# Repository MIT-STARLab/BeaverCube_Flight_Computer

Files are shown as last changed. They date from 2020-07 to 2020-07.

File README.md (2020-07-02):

# Note
This board is still under test, we will be updating system operational status as tests are completed.

# BFC
The BeaverCube Flight Computer, or CASTOR Pi Board, is an open-source flight computer for CubeSats. Designed for the MIT BeaverCube CubeSat mission, the board supports an imaging payload with 3 cameras over USB as well as subsystem boards over UART, I2C and SPI buses. 

CASTOR Pi Board: CubeSat Atmospheric and Sea-surface Temperature Optical Observation Raspberry Pi Board

# Known Issues, Testing Progress
The BFC rev 1.0 is currently being tested, with rev 2.0 expected to be manufactured and testing started by the end of August 2020. The power system has been characterized under expected loads and is fully operational with no errors detected. The RPI recovery system (see schematic Sheet 3) that controls which RPI is running and SD card is selected has been fully tested, and no errors detected.

The USB hub is currently under test to verify all ports can communicate with the compute module. Additional tests to be completed by mid-July 2020 include running flight software to verify all onboard devices (RTC, IMUs) function nominally, and interfacing the BFC with devices to test external connections including RS-485, TTL UART, I2C, SPI.

Known errors on rev 1.0 that will be fixed in rev 2.0
- SD card MUXs U4, U11, U13, U14 have incorrect footprints. The compute module cannot access the SD card slots.
- The USB line is routed to the incorrect GPIO pin on the compute module. A temporary fix was made to continue testing.

# project
Eagle CAD Project, Board, Schematic files.

# libraries
Ealgle CAD Library files.

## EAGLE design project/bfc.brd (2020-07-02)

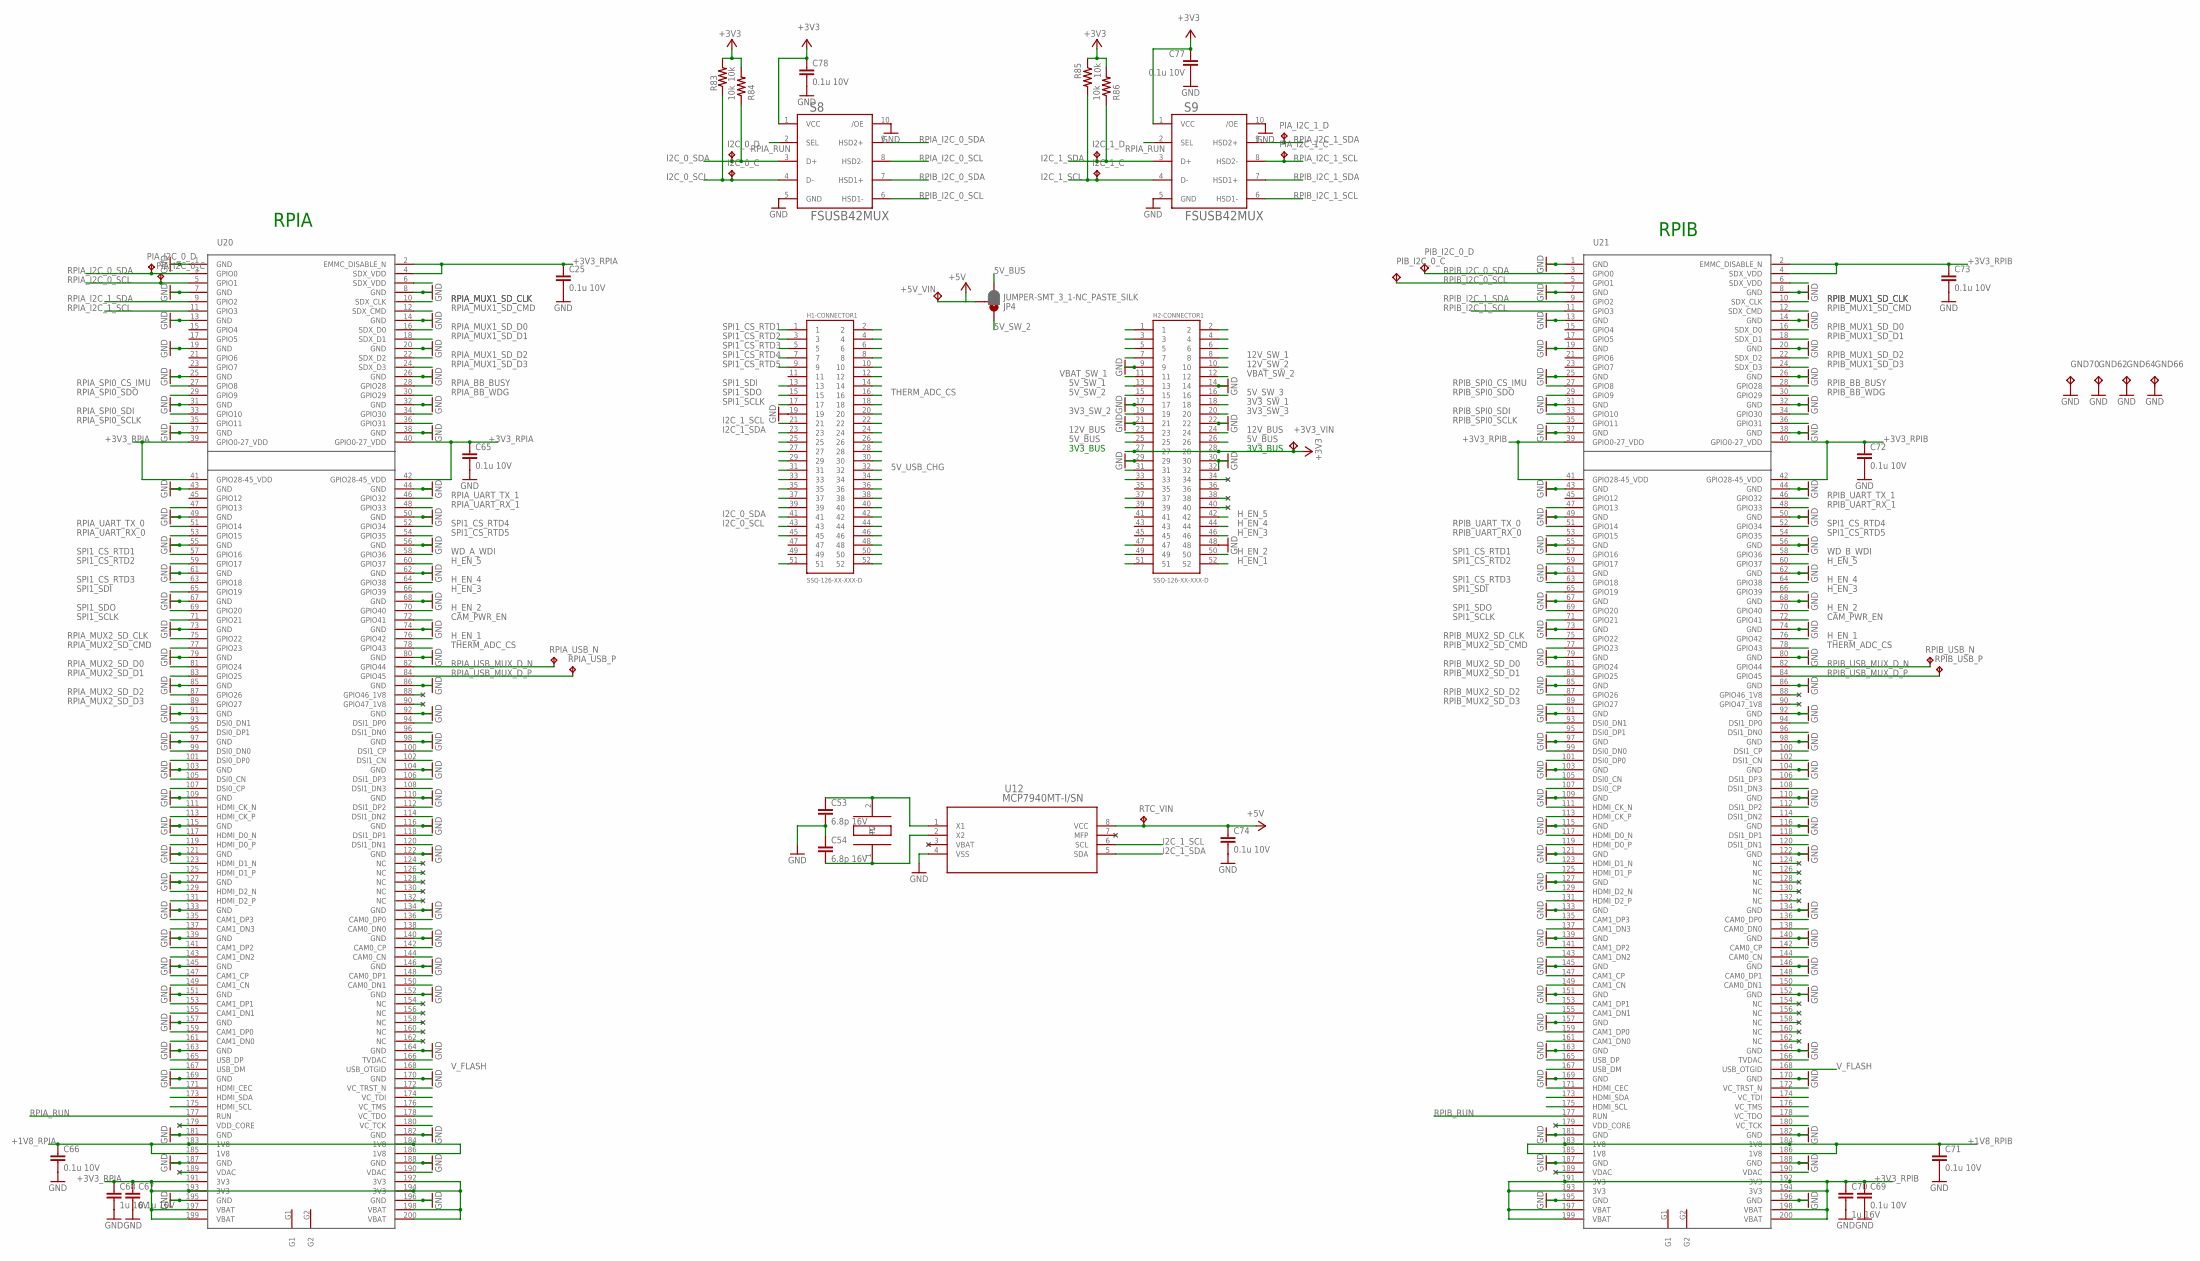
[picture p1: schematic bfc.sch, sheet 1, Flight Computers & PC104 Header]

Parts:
+3V3_VIN, +5V_VIN: TP_HRWN; MPN S2751-46R
C25, C65, C66, C67, C69, C71, C72, C73, C74, C77, C78: 0.1u 10V; C0603
C53, C54: 6.8p 16V; C0603
C68, C70: 1u 16V; C0603
GND62, GND64, GND66, GND70: TP_HRWN; MPN S2751-46R
H1-CONNECTOR1, H2-CONNECTOR1: SSQ-126-XX-XXX-D; MPN SSQ-126-23-G-D
I2C_0_C, I2C_0_D, I2C_1_C, I2C_1_D: TPB1,27; B1,27
JP4: JUMPER-SMT_3_1-NC_PASTE_SILK; SMT-JUMPER_3_1-NC_PASTE_SILK
PIA_I2C_0_C, PIA_I2C_0_D, PIA_I2C_1_C, PIA_I2C_1_D: TPB1,27; B1,27
PIB_I2C_0_C, PIB_I2C_0_D: TP_HRWN; MPN S2751-46R
R83, R84, R85, R86: 10k; R0603
RPIA_USB_N: TPB1,27; B1,27
RPIA_USB_P: TPB1,27; B1,27
RPIB_USB_N: TPB1,27; B1,27
RPIB_USB_P: TPB1,27; B1,27
RTC_VIN: TPB1,27; B1,27
S8, S9: FSUSB42MUX; MPN FSUSB42MUX
U12: MCP7940MT-I/SN; SOIC8-N_MC; MPN MCP7940MT-I/SN
U20, U21: COMPUTE_MODULE; SO-DIMM; MPN 1473005-4
X4: TC-135; MPN FC-135 32.768KA-AG0

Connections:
3V3_SW_1: H2-CONNECTOR1.18
3V3_SW_2: H2-CONNECTOR1.19; also elsewhere on the board
3V3_SW_3: H2-CONNECTOR1.20; also elsewhere on the board
5V_BUS: H2-CONNECTOR1.25, H2-CONNECTOR1.26, JP4.3; also elsewhere on the board
5V_SW_1: H2-CONNECTOR1.13
5V_SW_2: H2-CONNECTOR1.15, JP4.1
5V_SW_3: H2-CONNECTOR1.16
5V_USB_CHG: H1-CONNECTOR1.32
12V_BUS: H2-CONNECTOR1.23, H2-CONNECTOR1.24; also elsewhere on the board
12V_SW_1: H2-CONNECTOR1.8; also elsewhere on the board
12V_SW_2: H2-CONNECTOR1.10
+1V8_RPIA: C66.1, U20.183 (1V8), U20.184 (1V8), U20.185 (1V8), U20.186 (1V8); also elsewhere on the board
+1V8_RPIB: C71.1, U21.183 (1V8), U21.184 (1V8), U21.185 (1V8), U21.186 (1V8); also elsewhere on the board
+3V3: +3V3_VIN.P$1, C77.1, C78.1, H2-CONNECTOR1.27, H2-CONNECTOR1.28, R83.2, R84.2, R85.1, R86.2, S8.1 (VCC), S9.1 (VCC); also elsewhere on the board
+3V3_RPIA: C25.1, C65.1, C67.1, C68.1, U20.2 (EMMC_DISABLE_N), U20.4 (SDX_VDD), U20.39 (GPIO0-27_VDD), U20.40 (GPIO0-27_VDD), U20.41 (GPIO28-45_VDD), U20.42 (GPIO28-45_VDD), U20.191 (3V3), U20.192 (3V3), U20.193 (3V3), U20.194 (3V3), U20.197 (VBAT), U20.198 (VBAT), U20.199 (VBAT), U20.200 (VBAT); also elsewhere on the board
+3V3_RPIB: C69.1, C70.1, C72.1, C73.1, U21.2 (EMMC_DISABLE_N), U21.4 (SDX_VDD), U21.39 (GPIO0-27_VDD), U21.40 (GPIO0-27_VDD), U21.41 (GPIO28-45_VDD), U21.42 (GPIO28-45_VDD), U21.191 (3V3), U21.192 (3V3), U21.193 (3V3), U21.194 (3V3), U21.197 (VBAT), U21.198 (VBAT), U21.199 (VBAT), U21.200 (VBAT); also elsewhere on the board
+5V: +5V_VIN.P$1, C74.1, JP4.2, RTC_VIN.TP, U12.8 (VCC); also elsewhere on the board
CAM_PWR_EN: U20.72 (GPIO41), U21.72 (GPIO41); also elsewhere on the board
GND: C25.2, C53.2, C54.1, C65.2, C66.2, C67.2, C68.2, C69.2, C70.2, C71.2, C72.2, C73.2, C74.2, C77.2, C78.2, GND62.P$1, GND64.P$1, GND66.P$1, GND70.P$1, H1-CONNECTOR1.19, H2-CONNECTOR1.9, H2-CONNECTOR1.14, H2-CONNECTOR1.17, H2-CONNECTOR1.21, H2-CONNECTOR1.22, H2-CONNECTOR1.29, H2-CONNECTOR1.30, H2-CONNECTOR1.32, H2-CONNECTOR1.48, S8.5 (GND), S8.10 (/OE), S9.5 (GND), S9.10 (/OE), U12.4 (VSS), U20.1 (GND), U20.7 (GND), U20.8 (GND), U20.13 (GND), U20.14 (GND), U20.19 (GND), U20.20 (GND), U20.25 (GND), U20.26 (GND), U20.31 (GND), U20.32 (GND), U20.37 (GND), U20.38 (GND), U20.43 (GND), U20.44 (GND), U20.49 (GND), U20.50 (GND), U20.55 (GND), U20.56 (GND), U20.61 (GND), U20.62 (GND), U20.67 (GND), U20.68 (GND), U20.73 (GND), U20.74 (GND), U20.79 (GND), U20.80 (GND), U20.85 (GND), U20.86 (GND), U20.91 (GND), U20.92 (GND), U20.97 (GND), U20.98 (GND), U20.103 (GND), U20.104 (GND), U20.109 (GND), U20.110 (GND), U20.115 (GND), U20.116 (GND), U20.121 (GND), U20.122 (GND), U20.127 (GND), U20.133 (GND), U20.134 (GND), U20.139 (GND), U20.140 (GND), U20.145 (GND), U20.146 (GND), U20.151 (GND), U20.152 (GND), U20.157 (GND), U20.163 (GND), U20.164 (GND), U20.169 (GND), U20.170 (GND), U20.181 (GND), U20.182 (GND), U20.187 (GND), U20.188 (GND), U20.195 (GND), U20.196 (GND), U21.1 (GND), U21.7 (GND), U21.8 (GND), U21.13 (GND), U21.14 (GND), U21.19 (GND), U21.20 (GND), U21.25 (GND), U21.26 (GND), U21.31 (GND), U21.32 (GND), U21.37 (GND), U21.38 (GND), U21.43 (GND), U21.44 (GND), U21.49 (GND), U21.50 (GND), U21.55 (GND), U21.56 (GND), U21.61 (GND), U21.62 (GND), U21.67 (GND), U21.68 (GND), U21.73 (GND), U21.74 (GND), U21.79 (GND), U21.80 (GND), U21.85 (GND), U21.86 (GND), U21.91 (GND), U21.92 (GND), U21.97 (GND), U21.98 (GND), U21.103 (GND), U21.104 (GND), U21.109 (GND), U21.110 (GND), U21.115 (GND), U21.116 (GND), U21.121 (GND), U21.122 (GND), U21.127 (GND), U21.133 (GND), U21.134 (GND), U21.139 (GND), U21.140 (GND), U21.145 (GND), U21.146 (GND), U21.151 (GND), U21.152 (GND), U21.157 (GND), U21.163 (GND), U21.164 (GND), U21.169 (GND), U21.170 (GND), U21.181 (GND), U21.182 (GND), U21.187 (GND), U21.188 (GND), U21.195 (GND), U21.196 (GND); also elsewhere on the board
H_EN_1: H2-CONNECTOR1.52, U20.76 (GPIO42), U21.76 (GPIO42)
H_EN_2: H2-CONNECTOR1.50, U20.70 (GPIO40), U21.70 (GPIO40)
H_EN_3: H2-CONNECTOR1.46, U20.66 (GPIO39), U21.66 (GPIO39)
H_EN_4: H2-CONNECTOR1.44, U20.64 (GPIO38), U21.64 (GPIO38)
H_EN_5: H2-CONNECTOR1.42, U20.60 (GPIO37), U21.60 (GPIO37)
I2C_0_SCL: H1-CONNECTOR1.43, I2C_0_C.TP, R83.1, S8.4 (D-)
I2C_0_SDA: H1-CONNECTOR1.41, I2C_0_D.TP, R84.1, S8.3 (D+)
I2C_1_SCL: H1-CONNECTOR1.21, I2C_1_C.TP, R85.2, S9.4 (D-), U12.6 (SCL); also elsewhere on the board
I2C_1_SDA: H1-CONNECTOR1.23, I2C_1_D.TP, R86.1, S9.3 (D+), U12.5 (SDA); also elsewhere on the board
unnamed: C53.1, U12.1 (X1), X4.2
unnamed: C54.2, U12.2 (X2), X4.1
RPIA_BB_BUSY: U20.28 (GPIO28); also elsewhere on the board
RPIA_BB_WDG: U20.30 (GPIO29); also elsewhere on the board
RPIA_I2C_0_SCL: PIA_I2C_0_C.TP, S8.8 (HSD2-), U20.5 (GPIO1)
RPIA_I2C_0_SDA: PIA_I2C_0_D.TP, S8.9 (HSD2+), U20.3 (GPIO0)
RPIA_I2C_1_SCL: PIA_I2C_1_C.TP, S9.8 (HSD2-), U20.11 (GPIO3)
RPIA_I2C_1_SDA: PIA_I2C_1_D.TP, S9.9 (HSD2+), U20.9 (GPIO2)
RPIA_MUX1_SD_CLK: U20.10 (SDX_CLK); also elsewhere on the board
RPIA_MUX1_SD_CMD: U20.12 (SDX_CMD); also elsewhere on the board
RPIA_MUX1_SD_D0: U20.16 (SDX_D0); also elsewhere on the board
RPIA_MUX1_SD_D1: U20.18 (SDX_D1); also elsewhere on the board
RPIA_MUX1_SD_D2: U20.22 (SDX_D2); also elsewhere on the board
RPIA_MUX1_SD_D3: U20.24 (SDX_D3); also elsewhere on the board
RPIA_MUX2_SD_CLK: U20.75 (GPIO22); also elsewhere on the board
RPIA_MUX2_SD_CMD: U20.77 (GPIO23); also elsewhere on the board
RPIA_MUX2_SD_D0: U20.81 (GPIO24); also elsewhere on the board
RPIA_MUX2_SD_D1: U20.83 (GPIO25); also elsewhere on the board
RPIA_MUX2_SD_D2: U20.87 (GPIO26); also elsewhere on the board
RPIA_MUX2_SD_D3: U20.89 (GPIO27); also elsewhere on the board
RPIA_RUN: S8.2 (SEL), S9.2 (SEL), U20.177 (RUN); also elsewhere on the board
RPIA_SPI0_CS_IMU: U20.27 (GPIO8); also elsewhere on the board
RPIA_SPI0_SCLK: U20.35 (GPIO11); also elsewhere on the board
RPIA_SPI0_SDI: U20.33 (GPIO10); also elsewhere on the board
RPIA_SPI0_SDO: U20.29 (GPIO9); also elsewhere on the board
RPIA_UART_RX_0: U20.53 (GPIO15); also elsewhere on the board
RPIA_UART_RX_1: U20.48 (GPIO33); also elsewhere on the board
RPIA_UART_TX_0: U20.51 (GPIO14); also elsewhere on the board
RPIA_UART_TX_1: U20.46 (GPIO32); also elsewhere on the board
RPIA_USB_MUX_D_N: RPIA_USB_N.TP, U20.82 (GPIO44); also elsewhere on the board
RPIA_USB_MUX_D_P: RPIA_USB_P.TP, U20.84 (GPIO45); also elsewhere on the board
RPIB_BB_BUSY: U21.28 (GPIO28); also elsewhere on the board
RPIB_BB_WDG: U21.30 (GPIO29); also elsewhere on the board
RPIB_I2C_0_SCL: PIB_I2C_0_C.P$1, S8.6 (HSD1-), U21.5 (GPIO1)
RPIB_I2C_0_SDA: PIB_I2C_0_D.P$1, S8.7 (HSD1+), U21.3 (GPIO0)
RPIB_I2C_1_SCL: S9.6 (HSD1-), U21.11 (GPIO3)
RPIB_I2C_1_SDA: S9.7 (HSD1+), U21.9 (GPIO2)
RPIB_MUX1_SD_CLK: U21.10 (SDX_CLK); also elsewhere on the board
RPIB_MUX1_SD_CMD: U21.12 (SDX_CMD); also elsewhere on the board
RPIB_MUX1_SD_D0: U21.16 (SDX_D0); also elsewhere on the board
RPIB_MUX1_SD_D1: U21.18 (SDX_D1); also elsewhere on the board
RPIB_MUX1_SD_D2: U21.22 (SDX_D2); also elsewhere on the board
RPIB_MUX1_SD_D3: U21.24 (SDX_D3); also elsewhere on the board
RPIB_MUX2_SD_CLK: U21.75 (GPIO22); also elsewhere on the board
RPIB_MUX2_SD_CMD: U21.77 (GPIO23); also elsewhere on the board
RPIB_MUX2_SD_D0: U21.81 (GPIO24); also elsewhere on the board
RPIB_MUX2_SD_D1: U21.83 (GPIO25); also elsewhere on the board
RPIB_MUX2_SD_D2: U21.87 (GPIO26); also elsewhere on the board
RPIB_MUX2_SD_D3: U21.89 (GPIO27); also elsewhere on the board
RPIB_RUN: U21.177 (RUN); also elsewhere on the board
RPIB_SPI0_CS_IMU: U21.27 (GPIO8); also elsewhere on the board
RPIB_SPI0_SCLK: U21.35 (GPIO11); also elsewhere on the board
RPIB_SPI0_SDI: U21.33 (GPIO10); also elsewhere on the board
RPIB_SPI0_SDO: U21.29 (GPIO9); also elsewhere on the board
RPIB_UART_RX_0: U21.53 (GPIO15); also elsewhere on the board
RPIB_UART_RX_1: U21.48 (GPIO33); also elsewhere on the board
RPIB_UART_TX_0: U21.51 (GPIO14); also elsewhere on the board
RPIB_UART_TX_1: U21.46 (GPIO32); also elsewhere on the board
RPIB_USB_MUX_D_N: RPIB_USB_N.TP, U21.82 (GPIO44); also elsewhere on the board
RPIB_USB_MUX_D_P: RPIB_USB_P.TP, U21.84 (GPIO45); also elsewhere on the board
SPI1_CS_RTD1: H1-CONNECTOR1.1, U20.57 (GPIO16), U21.57 (GPIO16)
SPI1_CS_RTD2: H1-CONNECTOR1.3, U20.59 (GPIO17), U21.59 (GPIO17)
SPI1_CS_RTD3: H1-CONNECTOR1.5, U20.63 (GPIO18), U21.63 (GPIO18)
SPI1_CS_RTD4: H1-CONNECTOR1.7, U20.52 (GPIO34), U21.52 (GPIO34)
SPI1_CS_RTD5: H1-CONNECTOR1.9, U20.54 (GPIO35), U21.54 (GPIO35)
SPI1_SCLK: H1-CONNECTOR1.17, U20.71 (GPIO21), U21.71 (GPIO21)
SPI1_SDI: H1-CONNECTOR1.13, U20.65 (GPIO19), U21.65 (GPIO19)
SPI1_SDO: H1-CONNECTOR1.15, U20.69 (GPIO20), U21.69 (GPIO20)
THERM_ADC_CS: H1-CONNECTOR1.16, U20.78 (GPIO43), U21.78 (GPIO43)
VBAT: U12.3 (VBAT)
VBAT_SW_1: H2-CONNECTOR1.11
VBAT_SW_2: H2-CONNECTOR1.12
V_FLASH: U20.168 (USB_OTGID), U21.168 (USB_OTGID); also elsewhere on the board
WD_A_WDI: U20.58 (GPIO36); also elsewhere on the board
WD_B_WDI: U21.58 (GPIO36); also elsewhere on the board

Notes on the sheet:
RPIA
RPIB
3V3_BUS

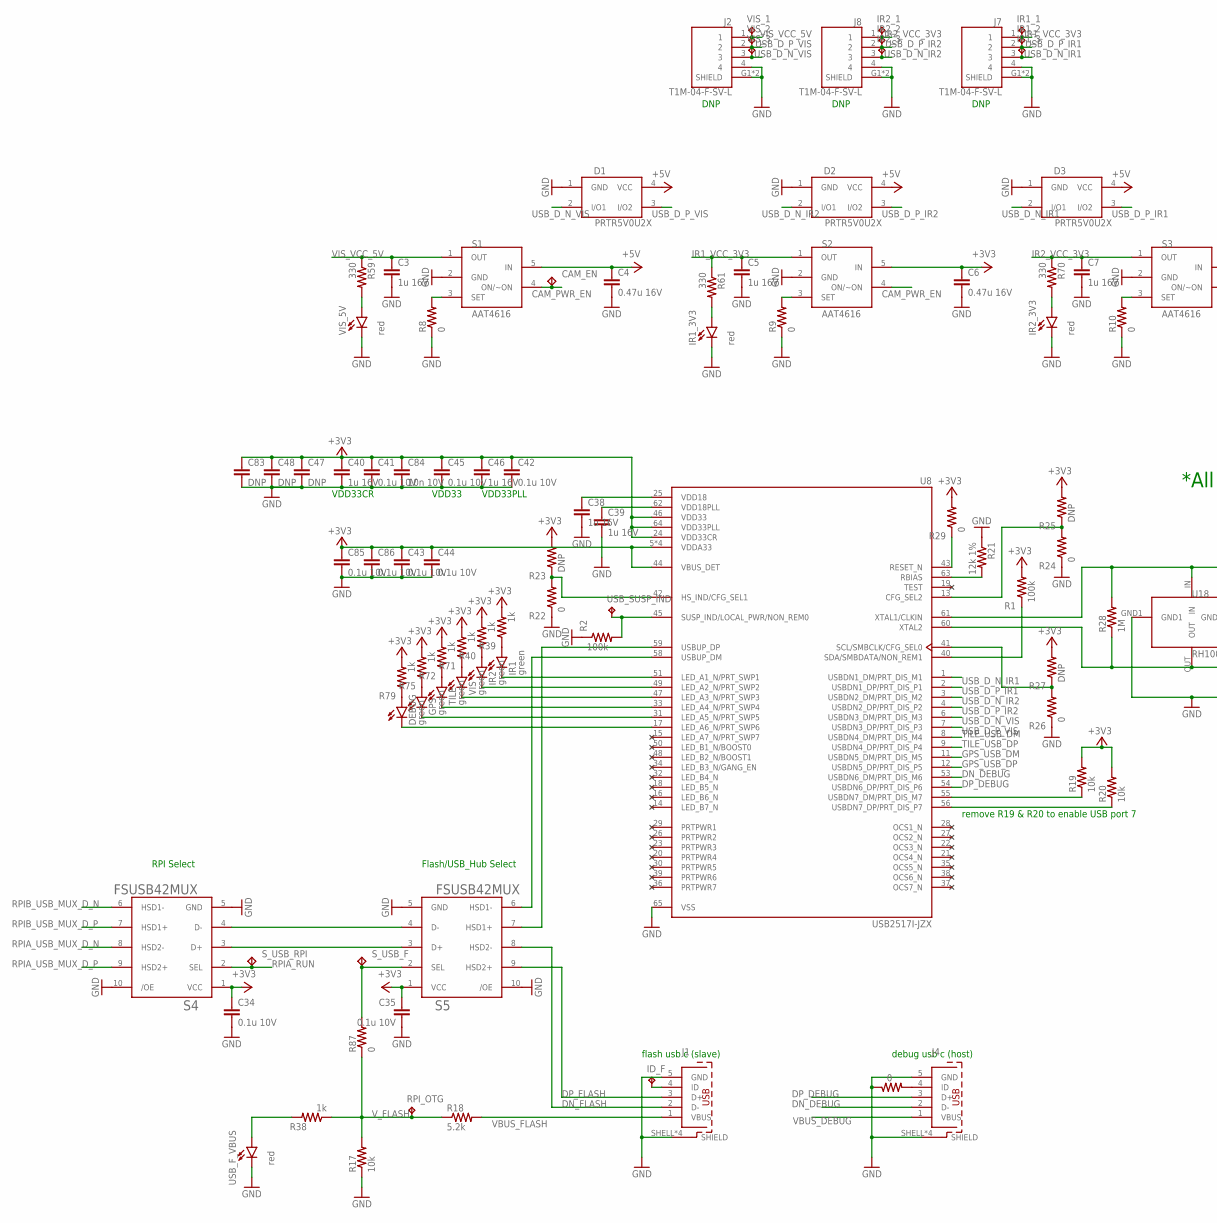
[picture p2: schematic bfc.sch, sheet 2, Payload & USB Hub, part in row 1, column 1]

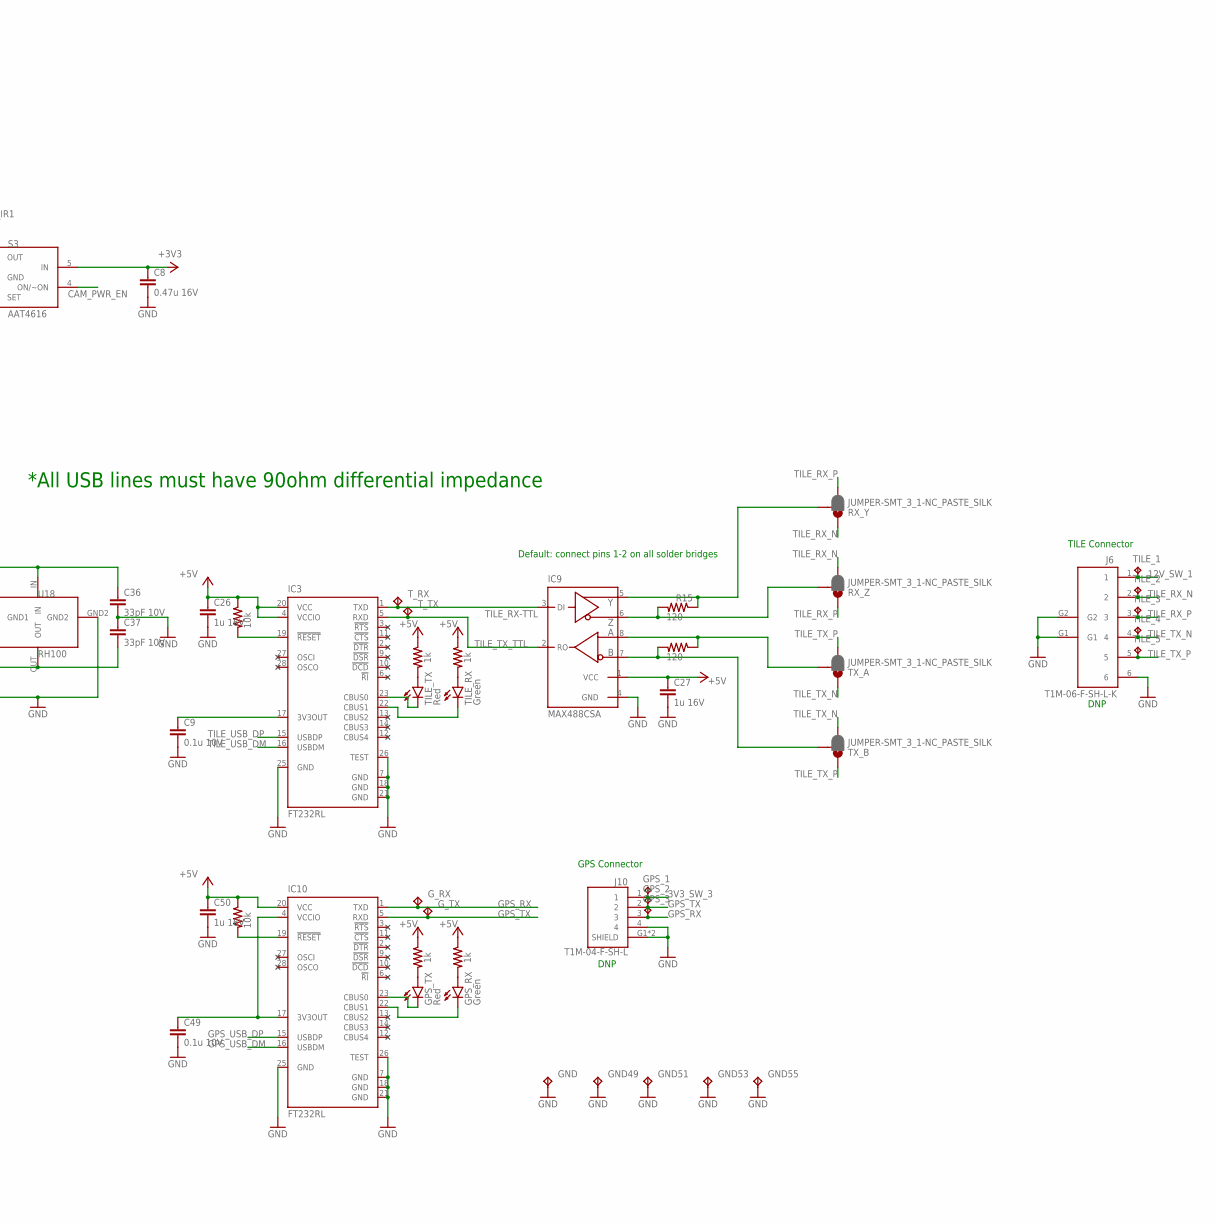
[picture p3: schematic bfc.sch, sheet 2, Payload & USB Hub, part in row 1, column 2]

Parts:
C3, C5, C7, C26, C27, C38, C39, C40, C46, C50: 1u 16V; C0603
C4, C6, C8: 0.47u 16V; C0603
C9, C34, C35, C41, C42, C43, C44, C45, C49, C85, C86: 0.1u 10V; C0603
C36, C37: 33pF 10V; C0603
C47, C48, C83: DNP; C0603
C84: 10n 10V; C0603
CAM_EN: TP_HRWN
D1, D2, D3: PRTR5V0U2X; MPN PRTR5V0U2X,215
DEBUG: green; SML0603; MPN LG L29K-F2J1-24-Z
GND, GND49, GND51, GND53, GND55: TP_HRWN
GPS: green; SML0603; MPN LG L29K-F2J1-24-Z
GPS_1, GPS_2, GPS_3: TPTP15SQ; TP15SQ
GPS_RX: Green; SML0603; MPN 150060VS75000
GPS_TX: Red; SML0603; MPN LTST-C190CKT
G_RX: TP_HRWN
G_TX: TP_HRWN
IC3, IC10: FT232RL; SSOP28
IC9: MAX488CSA; SO08; MPN MAX488ESA+
ID_F: TPTP18SQ; TP18SQ
IR1, IR2: green; SML0603; MPN LG L29K-F2J1-24-Z
IR1_1, IR1_2, IR1_3, IR2_1, IR2_2, IR2_3: TPTP15SQ; TP15SQ
IR1_3V3, IR2_3V3: red; SML0603; MPN LTST-C190CKT
J1, J4: 629105150521; MPN 629105150521
J2, J7, J8: T1M-04-F-SV-L; SAMTEC_T1M-04-F-SV-L; MPN T1M-04-F-SV-L
J6: T1M-06-F-SH-L-K; MPN T1M-06-F-SH-L
J10: T1M-04-F-SH-L; SAMTEC_T1M-04-F-SH-L; MPN T1M-04-F-SH-L
R1, R2: 100k; R0603
R8, R9, R10, R24, R26, R37: 0; R0603
R11, R17, R19, R20, R31: 10k; R0603
R12, R30, R32, R33, R38, R39, R40, R71, R72, R75, R79: 1k; R0603
R15, R16: 120; R0603
R18: 5.2k; R0805
R21: 12k 1%; R0603
R22, R29, R87: 0; R0805
R23: DNP; R0805
R25, R27: DNP; R0603
R28: 1M; R0603
R59, R61, R70: 330; R0603
RPI_OTG: TPB1,27; B1,27
RX_Y: JUMPER-SMT_3_1-NC_PASTE_SILK; SMT-JUMPER_3_1-NC_PASTE_SILK
RX_Z: JUMPER-SMT_3_1-NC_PASTE_SILK; SMT-JUMPER_3_1-NC_PASTE_SILK
S1, S2, S3: AAT4616; MPN AAT4616IGV-T1
S4, S5: FSUSB42MUX; MPN FSUSB42MUX
S_USB_F: TP_HRWN
S_USB_RPI: TP_HRWN
TILE: green; SML0603; MPN LG L29K-F2J1-24-Z
TILE_1, TILE_2, TILE_3, TILE_4, TILE_5: TPTP15SQ; TP15SQ
TILE_RX: Green; SML0603; MPN 150060VS75000
TILE_TX: Red; SML0603; MPN LTST-C190CKT
TX_A: JUMPER-SMT_3_1-NC_PASTE_SILK; SMT-JUMPER_3_1-NC_PASTE_SILK
TX_B: JUMPER-SMT_3_1-NC_PASTE_SILK; SMT-JUMPER_3_1-NC_PASTE_SILK
T_RX: TP_HRWN
T_TX: TP_HRWN
U8: USB2517I-JZX; QFN50P900X900X100-65N; MPN USB2517I-JZX-TR
U18: RH100; MPN RH100-24.000-20-3050-EXT-TR
USB_F_VBUS: red; SML0603; MPN LTST-C190CKT
USB_SUSP_IND: TPTP18SQ; TP18SQ
VIS: green; SML0603; MPN LG L29K-F2J1-24-Z
VIS_1, VIS_2, VIS_3: TPTP15SQ; TP15SQ
VIS_5V: red; SML0603; MPN LTST-C190CKT

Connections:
3V3_SW_3: GPS_1.TP, J10.1; also elsewhere on the board
12V_SW_1: J6.1, TILE_1.TP; also elsewhere on the board
+3V3: C6.1, C8.1, C34.1, C35.1, C40.1, C41.1, C42.1, C43.1, C44.1, C45.1, C46.1, C47.1, C48.1, C83.1, C84.1, C85.1, C86.1, R1.2, R19.2, R20.2, R23.2, R25.2, R27.2, R29.2, R39.2, R40.2, R71.2, R72.2, R75.2, R79.2, S2.5 (IN), S3.5 (IN), S4.1 (VCC), S5.1 (VCC), U8.5 (VDDA33), U8.10 (VDDA33), U8.24 (VDD33CR), U8.44 (VBUS_DET), U8.46 (VDD33), U8.52 (VDDA33), U8.57 (VDDA33), U8.64 (VDD33PLL); also elsewhere on the board
+5V: C4.1, C26.1, C27.1, C50.1, D1.4 (VCC), D2.4 (VCC), D3.4 (VCC), IC3.4 (VCCIO), IC3.20 (VCC), IC9.1 (VCC), IC10.20 (VCC), R11.1, R12.1, R30.1, R31.1, R32.1, R33.1, S1.5 (IN); also elsewhere on the board
CAM_PWR_EN: CAM_EN.P$1, S1.4 (ON/~ON), S2.4 (ON/~ON), S3.4 (ON/~ON); also elsewhere on the board
DN_DEBUG: J4.2 (D-), U8.53 (USBDN6_DM/PRT_DIS_M6)
DN_FLASH: J1.2 (D-), S5.8 (HSD2-)
DP_DEBUG: J4.3 (D+), U8.54 (USBDN6_DP/PRT_DIS_P6)
DP_FLASH: J1.3 (D+), S5.9 (HSD2+)
GND: C3.2, C4.2, C5.2, C6.2, C7.2, C8.2, C9.2, C26.2, C27.2, C34.2, C35.2, C36.2, C37.1, C38.2, C39.2, C40.2, C41.2, C42.2, C43.2, C44.2, C45.2, C46.2, C47.2, C48.2, C49.2, C50.2, C83.2, C84.2, C85.2, C86.2, D1.1 (GND), D2.1 (GND), D3.1 (GND), GND.P$1, GND49.P$1, GND51.P$1, GND53.P$1, GND55.P$1, IC3.7 (GND), IC3.18 (GND), IC3.21 (GND), IC3.25 (GND), IC3.26 (TEST), IC9.4 (GND), IC10.7 (GND), IC10.18 (GND), IC10.21 (GND), IC10.25 (GND), IC10.26 (TEST), IR1_3V3.C, IR2_3V3.C, J1.5 (GND), J1.SHELL (SHIELD), J1.SHELL1 (SHIELD), J1.SHELL2 (SHIELD), J1.SHELL3 (SHIELD), J2.4, J2.G1 (SHIELD), J2.G2 (SHIELD), J4.5 (GND), J4.SHELL (SHIELD), J4.SHELL1 (SHIELD), J4.SHELL2 (SHIELD), J4.SHELL3 (SHIELD), J6.6, J6.G1, J6.G2, J7.4, J7.G1 (SHIELD), J7.G2 (SHIELD), J8.4, J8.G1 (SHIELD), J8.G2 (SHIELD), J10.4, J10.G1 (SHIELD), J10.G2 (SHIELD), R2.1, R8.1, R9.1, R10.1, R17.1, R21.1, R22.1, R24.1, R26.1, R37.1, S1.2 (GND), S2.2 (GND), S3.2 (GND), S4.5 (GND), S4.10 (/OE), S5.5 (GND), S5.10 (/OE), U8.65 (VSS), U18.GND1, U18.GND2, USB_F_VBUS.C, VIS_5V.C; also elsewhere on the board
GPS_RX: GPS_3.TP, G_RX.P$1, IC10.1 (TXD), J10.3
GPS_TX: GPS_2.TP, G_TX.P$1, IC10.5 (RXD), J10.2
GPS_USB_DM: IC10.16 (USBDM), U8.11 (USBDN5_DM/PRT_DIS_M5)
GPS_USB_DP: IC10.15 (USBDP), U8.12 (USBDN5_DP/PRT_DIS_P5)
IR1_VCC_3V3: C5.1, IR1_1.TP, J7.1, R61.1, S2.1 (OUT)
IR2_VCC_3V3: C7.1, IR2_1.TP, J8.1, R70.1, S3.1 (OUT)
unnamed: R10.2, S3.3 (SET)
unnamed: R8.2, S1.3 (SET)
unnamed: R9.2, S2.3 (SET)
unnamed: R22.2, R23.1, U8.42 (HS_IND/CFG_SEL1)
unnamed: J4.4 (ID), R37.2
unnamed: R38.2, USB_F_VBUS.A
unnamed: IR1.A, R39.1
unnamed: IR1.C, U8.51 (LED_A1_N/PRT_SWP1)
unnamed: IC3.19 (!RESET), R11.2
unnamed: R12.2, TILE_TX.A
unnamed: R30.2, TILE_RX.A
unnamed: IC3.23 (CBUS0), TILE_TX.C
unnamed: IC9.7 (B), R16.2, TX_B.2
unnamed: IC3.22 (CBUS1), TILE_RX.C
unnamed: C9.1, IC3.17 (3V3OUT)
unnamed: IC10.19 (!RESET), R31.2
unnamed: GPS_TX.A, R32.2
unnamed: IR2.C, U8.49 (LED_A2_N/PRT_SWP2)
unnamed: IR2.A, R40.1
unnamed: R71.1, VIS.A
unnamed: R72.1, TILE.A
unnamed: GPS.A, R75.1
unnamed: DEBUG.A, R79.1
unnamed: U8.47 (LED_A3_N/PRT_SWP3), VIS.C
unnamed: TILE.C, U8.33 (LED_A4_N/PRT_SWP4)
unnamed: GPS.C, U8.31 (LED_A5_N/PRT_SWP5)
unnamed: R21.2, U8.63 (RBIAS)
unnamed: DEBUG.C, U8.17 (LED_A6_N/PRT_SWP6)
unnamed: R87.2, S5.2 (SEL), S_USB_F.P$1
unnamed: IC9.5 (Y), R15.1, RX_Y.2
unnamed: GPS_RX.A, R33.2
unnamed: GPS_TX.C, IC10.23 (CBUS0)
unnamed: GPS_RX.C, IC10.22 (CBUS1)
unnamed: ID_F.TP, J1.4 (ID)
unnamed: R1.1, U8.40 (SDA/SMBDATA/NON_REM1)
unnamed: S4.3 (D+), S5.3 (D+)
unnamed: S4.4 (D-), S5.4 (D-)
unnamed: R26.2, R27.1, U8.41 (SCL/SMBCLK/CFG_SEL0)
unnamed: S5.6 (HSD1-), U8.58 (USBUP_DM)
unnamed: S5.7 (HSD1+), U8.59 (USBUP_DP)
unnamed: R19.1, U8.55 (USBDN7_DM/PRT_DIS_M7)
unnamed: R20.1, U8.56 (USBDN7_DP/PRT_DIS_P7)
unnamed: R24.2, R25.1, U8.13 (CFG_SEL2)
unnamed: C36.1, R28.2, U8.61 (XTAL1/CLKIN), U18.IN
unnamed: C49.1, IC10.4 (VCCIO), IC10.17 (3V3OUT)
unnamed: C38.1, U8.25 (VDD18)
unnamed: C37.2, R28.1, U8.60 (XTAL2), U18.OUT
unnamed: C39.1, U8.62 (VDD18PLL)
unnamed: R2.2, U8.45 (SUSP_IND/LOCAL_PWR/NON_REM0), USB_SUSP_IND.TP
unnamed: R29.1, U8.43 (RESET_N)
unnamed: IC9.6 (Z), R15.2, RX_Z.2
unnamed: IC9.8 (A), R16.1, TX_A.2
unnamed: IR1_3V3.A, R61.2
unnamed: IR2_3V3.A, R70.2
unnamed: R59.2, VIS_5V.A
RPIA_RUN: S4.2 (SEL), S_USB_RPI.P$1; also elsewhere on the board
RPIA_USB_MUX_D_N: S4.8 (HSD2-); also elsewhere on the board
RPIA_USB_MUX_D_P: S4.9 (HSD2+); also elsewhere on the board
RPIB_USB_MUX_D_N: S4.6 (HSD1-); also elsewhere on the board
RPIB_USB_MUX_D_P: S4.7 (HSD1+); also elsewhere on the board
TILE_RX-TTL: IC3.1 (TXD), IC9.3 (DI), T_RX.P$1
TILE_RX_N: J6.2, RX_Y.1, RX_Z.3, TILE_2.TP
TILE_RX_P: J6.3, RX_Y.3, RX_Z.1, TILE_3.TP
TILE_TX_N: J6.4, TILE_4.TP, TX_A.1, TX_B.3
TILE_TX_P: J6.5, TILE_5.TP, TX_A.3, TX_B.1
TILE_TX_TTL: IC3.5 (RXD), IC9.2 (RO), T_TX.P$1
TILE_USB_DM: IC3.16 (USBDM), U8.8 (USBDN4_DM/PRT_DIS_M4)
TILE_USB_DP: IC3.15 (USBDP), U8.9 (USBDN4_DP/PRT_DIS_P4)
USB_D_N_IR1: D3.2 (I/O1), IR1_3.TP, J7.3, U8.1 (USBDN1_DM/PRT_DIS_M1)
USB_D_N_IR2: D2.2 (I/O1), IR2_3.TP, J8.3, U8.3 (USBDN2_DM/PRT_DIS_M2)
USB_D_N_VIS: D1.2 (I/O1), J2.3, U8.6 (USBDN3_DM/PRT_DIS_M3), VIS_3.TP
USB_D_P_IR1: D3.3 (I/O2), IR1_2.TP, J7.2, U8.2 (USBDN1_DP/PRT_DIS_P1)
USB_D_P_IR2: D2.3 (I/O2), IR2_2.TP, J8.2, U8.4 (USBDN2_DP/PRT_DIS_P2)
USB_D_P_VIS: D1.3 (I/O2), J2.2, U8.7 (USBDN3_DP/PRT_DIS_P3), VIS_2.TP
VBUS_DEBUG: J4.1 (VBUS)
VBUS_FLASH: J1.1 (VBUS), R18.2
VIS_VCC_5V: C3.1, J2.1, R59.1, S1.1 (OUT), VIS_1.TP
V_FLASH: R17.2, R18.1, R38.1, R87.1, RPI_OTG.TP; also elsewhere on the board

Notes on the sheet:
Flash/USB_Hub Select
RPI Select
remove R19 & R20 to enable USB port 7
Default: connect pins 1-2 on all solder bridges
debug usb c (host)
*All USB lines must have 90ohm differential impedance
TILE Connector
GPS Connector
VDD33CR
VDD33
VDD33PLL
flash usb c (slave)
DNP

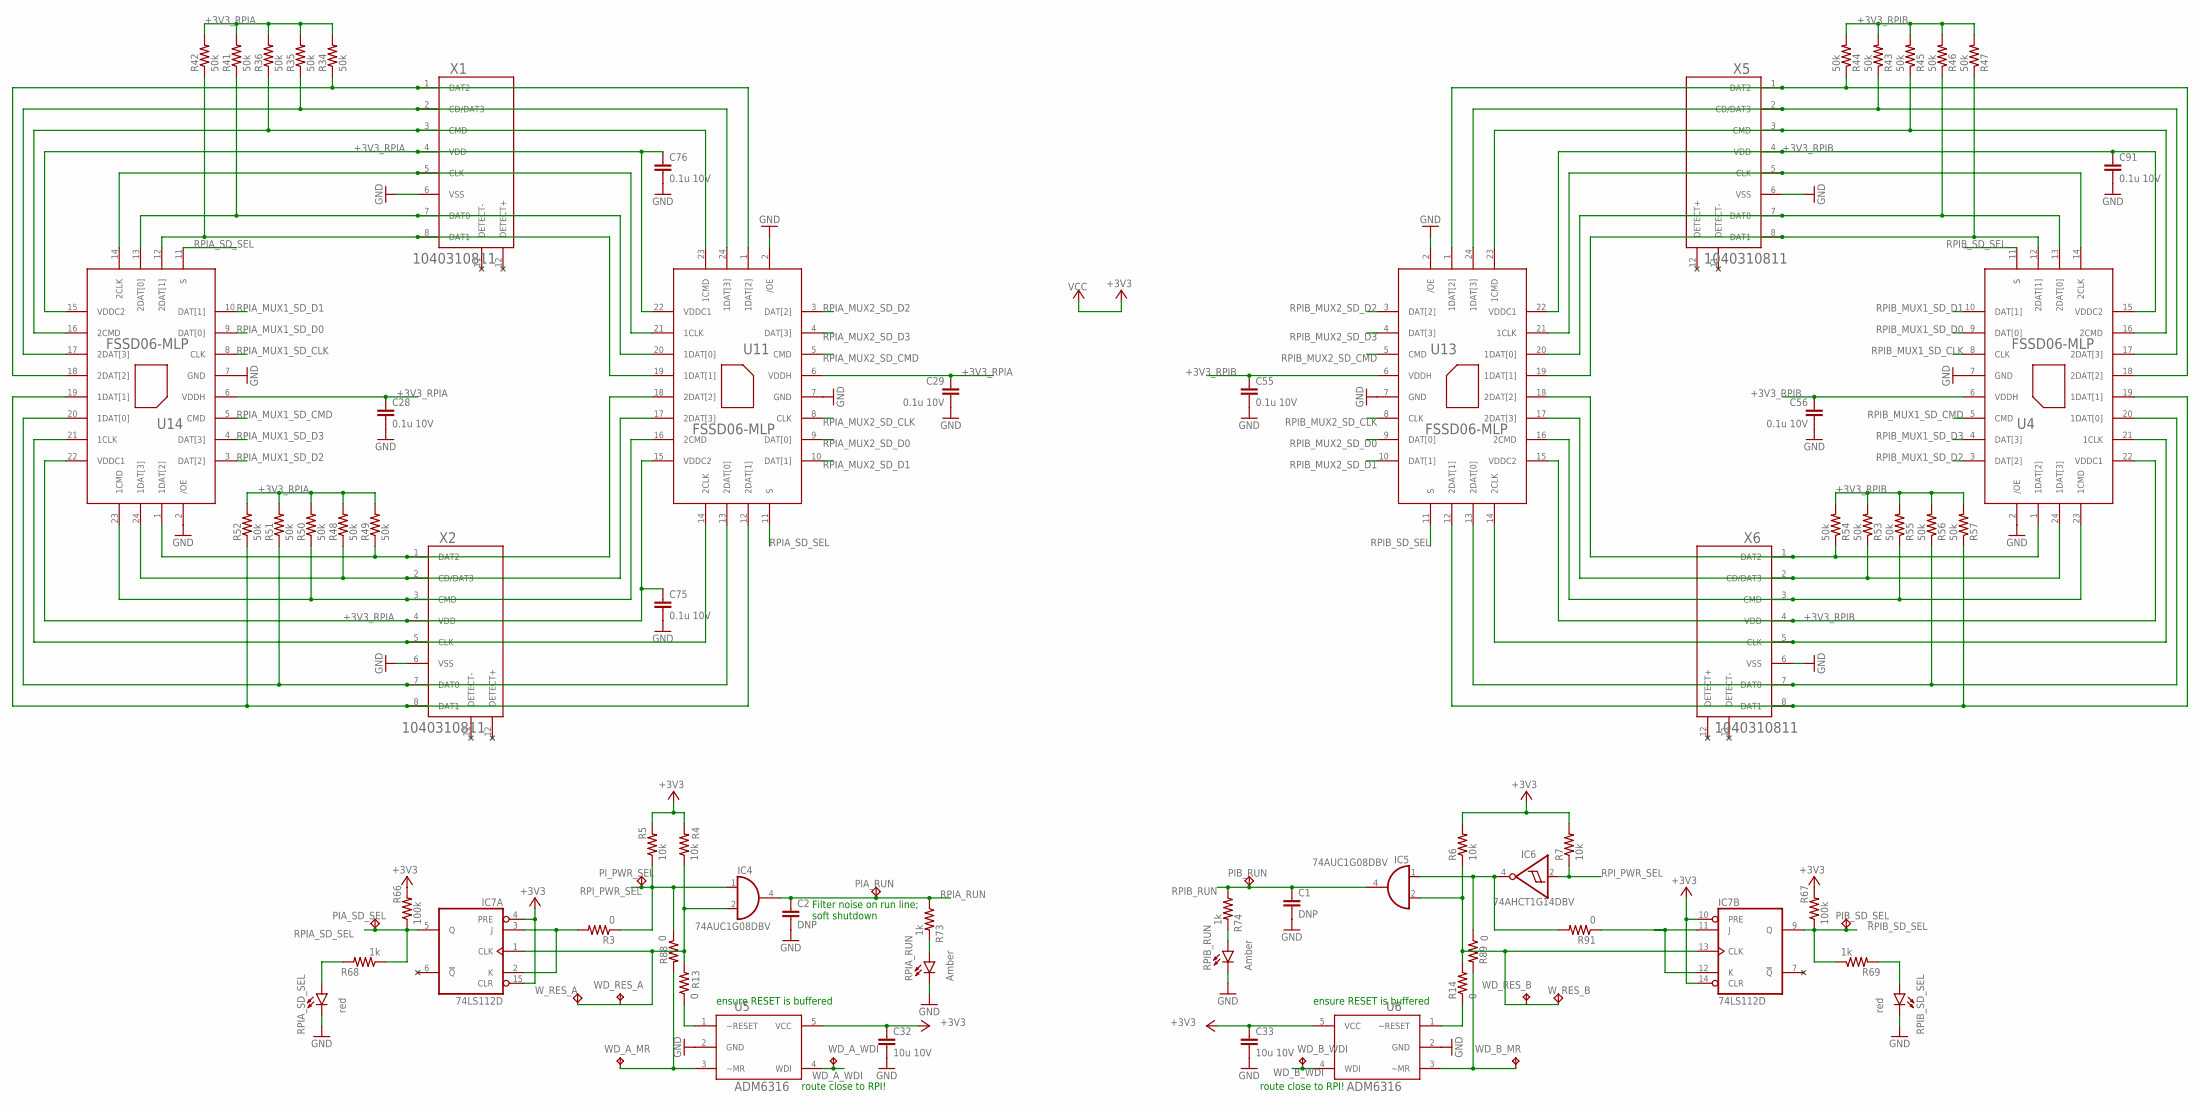
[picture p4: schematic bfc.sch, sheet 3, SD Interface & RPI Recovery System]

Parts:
C1, C2: DNP; C0603
C28, C29, C55, C56, C75, C76, C91: 0.1u 10V; C0603
C32, C33: 10u 10V; C0805
IC4, IC5: 74AUC1G08DBV; SOT23-5; MPN SN74LVC1G08MDBVREP
IC6: 74AHCT1G14DBV; SOT23-5; MPN SN74LVC1G14MDBVREP
IC7: 74LS112D; SO16; MPN SN74LVC112ADR
PIA_RUN: TP_HRWN; MPN S2751-46R
PIA_SD_SEL: TP_HRWN; MPN S2751-46R
PIB_RUN: TP_HRWN; MPN S2751-46R
PIB_SD_SEL: TP_HRWN; MPN S2751-46R
PI_PWR_SEL: TP_HRWN; MPN S2751-46R
R3, R13, R14, R88, R89, R91: 0; R0603
R4, R5, R6, R7: 10k; R0603
R34, R35, R36, R41, R42, R43, R44, R45, R46, R47, R48, R49, R50, R51, R52, R53, R54, R55, R56, R57: 50k; R0603
R66, R67: 100k; R0603
R68, R69, R73, R74: 1k; R0603
RPIA_RUN: Amber; SML0603; MPN SM0805AC
RPIA_SD_SEL: red; SML0603; MPN LTST-C190CKT
RPIB_RUN: Amber; SML0603; MPN SM0805AC
RPIB_SD_SEL: red; SML0603; MPN LTST-C190CKT
U4, U11, U13, U14: FSSD06-MLP; MPN FSSD06BQX
U5, U6: ADM6316; AMD6316; MPN ADM6320CZ29ARJZ-R7
WD_A_MR: TPTP18SQ; TP18SQ
WD_A_WDI: TPB1,27; B1,27
WD_B_MR: TPTP18SQ; TP18SQ
WD_B_WDI: TPB1,27; B1,27
WD_RES_A: TPTP18SQ; TP18SQ
WD_RES_B: TPTP18SQ; TP18SQ
W_RES_A: TP_HRWN; MPN S2751-46R
W_RES_B: TP_HRWN; MPN S2751-46R
X1, X2, X5, X6: 1040310811; MPN 1040310811

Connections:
+3V3: C32.1, C33.1, IC4.5 (VCC), IC5.5 (VCC), IC6.5 (VCC), IC7.4 (PRE), IC7.10 (PRE), IC7.14 (CLR), IC7.15 (CLR), IC7.16 (VCC), R4.2, R5.2, R6.2, R7.2, R66.2, R67.2, U5.5 (VCC), U6.5 (VCC); also elsewhere on the board
+3V3_RPIA: C28.1, C29.1, C75.1, C76.1, R34.2, R35.2, R36.2, R41.2, R42.2, R48.2, R49.2, R50.2, R51.2, R52.2, U11.6 (VDDH), U11.15 (VDDC2), U11.22 (VDDC1), U14.6 (VDDH), U14.15 (VDDC2), U14.22 (VDDC1), X1.4 (VDD), X2.4 (VDD); also elsewhere on the board
+3V3_RPIB: C55.1, C56.1, C91.1, R43.2, R44.2, R45.2, R46.2, R47.2, R53.2, R54.2, R55.2, R56.2, R57.2, U4.6 (VDDH), U4.15 (VDDC2), U4.22 (VDDC1), U13.6 (VDDH), U13.15 (VDDC2), U13.22 (VDDC1), X5.4 (VDD), X6.4 (VDD); also elsewhere on the board
GND: C1.2, C2.2, C28.2, C29.2, C32.2, C33.2, C55.2, C56.2, C75.2, C76.2, C91.2, IC4.3 (GND), IC5.3 (GND), IC6.3 (GND), IC7.8 (GND), RPIA_RUN.C, RPIA_SD_SEL.C, RPIB_RUN.C, RPIB_SD_SEL.C, U4.2 (/OE), U4.7 (GND), U5.2 (GND), U6.2 (GND), U11.2 (/OE), U11.7 (GND), U13.2 (/OE), U13.7 (GND), U14.2 (/OE), U14.7 (GND), X1.6 (VSS), X2.6 (VSS), X5.6 (VSS), X6.6 (VSS); also elsewhere on the board
unnamed: R34.1, U11.1 (1DAT[2]), U14.18 (2DAT[2]), X1.1 (DAT2)
unnamed: R35.1, U11.24 (1DAT[3]), U14.17 (2DAT[3]), X1.2 (CD/DAT3)
unnamed: R36.1, U11.23 (1CMD), U14.16 (2CMD), X1.3 (CMD)
unnamed: IC7.2 (K), IC7.3 (J), R3.2
unnamed: IC7.11 (J), IC7.12 (K), R91.1
unnamed: R88.2, U5.3 (~MR), WD_A_MR.TP
unnamed: R89.2, U6.3 (~MR), WD_B_MR.TP
unnamed: U11.21 (1CLK), U14.14 (2CLK), X1.5 (CLK)
unnamed: R41.1, U11.20 (1DAT[0]), U14.13 (2DAT[0]), X1.7 (DAT0)
unnamed: R42.1, U11.19 (1DAT[1]), U14.12 (2DAT[1]), X1.8 (DAT1)
unnamed: IC4.2 (I1), IC7.1 (CLK), R4.1, R13.2, WD_RES_A.TP, W_RES_A.P$1
unnamed: IC5.2 (I1), IC7.13 (CLK), R6.1, R14.2, WD_RES_B.TP, W_RES_B.P$1
unnamed: IC5.1 (I0), IC6.4 (O), R89.1, R91.2
unnamed: R48.1, U11.17 (2DAT[3]), U14.24 (1DAT[3]), X2.2 (CD/DAT3)
unnamed: R50.1, U11.16 (2CMD), U14.23 (1CMD), X2.3 (CMD)
unnamed: U11.14 (2CLK), U14.21 (1CLK), X2.5 (CLK)
unnamed: R51.1, U11.13 (2DAT[0]), U14.20 (1DAT[0]), X2.7 (DAT0)
unnamed: R13.1, U5.1 (~RESET)
unnamed: R14.1, U6.1 (~RESET)
unnamed: R52.1, U11.12 (2DAT[1]), U14.19 (1DAT[1]), X2.8 (DAT1)
unnamed: R49.1, U11.18 (2DAT[2]), U14.1 (1DAT[2]), X2.1 (DAT2)
unnamed: R44.1, U4.18 (2DAT[2]), U13.1 (1DAT[2]), X5.1 (DAT2)
unnamed: R43.1, U4.17 (2DAT[3]), U13.24 (1DAT[3]), X5.2 (CD/DAT3)
unnamed: R45.1, U4.16 (2CMD), U13.23 (1CMD), X5.3 (CMD)
unnamed: U4.14 (2CLK), U13.21 (1CLK), X5.5 (CLK)
unnamed: R46.1, U4.13 (2DAT[0]), U13.20 (1DAT[0]), X5.7 (DAT0)
unnamed: R47.1, U4.12 (2DAT[1]), U13.19 (1DAT[1]), X5.8 (DAT1)
unnamed: R53.1, U4.24 (1DAT[3]), U13.17 (2DAT[3]), X6.2 (CD/DAT3)
unnamed: R55.1, U4.23 (1CMD), U13.16 (2CMD), X6.3 (CMD)
unnamed: U4.21 (1CLK), U13.14 (2CLK), X6.5 (CLK)
unnamed: R56.1, U4.20 (1DAT[0]), U13.13 (2DAT[0]), X6.7 (DAT0)
unnamed: R57.1, U4.19 (1DAT[1]), U13.12 (2DAT[1]), X6.8 (DAT1)
unnamed: R54.1, U4.1 (1DAT[2]), U13.18 (2DAT[2]), X6.1 (DAT2)
unnamed: R68.2, RPIA_SD_SEL.A
unnamed: R69.2, RPIB_SD_SEL.A
unnamed: R73.2, RPIA_RUN.A
unnamed: R74.2, RPIB_RUN.A
RPIA_MUX1_SD_CLK: U14.8 (CLK); also elsewhere on the board
RPIA_MUX1_SD_CMD: U14.5 (CMD); also elsewhere on the board
RPIA_MUX1_SD_D0: U14.9 (DAT[0]); also elsewhere on the board
RPIA_MUX1_SD_D1: U14.10 (DAT[1]); also elsewhere on the board
RPIA_MUX1_SD_D2: U14.3 (DAT[2]); also elsewhere on the board
RPIA_MUX1_SD_D3: U14.4 (DAT[3]); also elsewhere on the board
RPIA_MUX2_SD_CLK: U11.8 (CLK); also elsewhere on the board
RPIA_MUX2_SD_CMD: U11.5 (CMD); also elsewhere on the board
RPIA_MUX2_SD_D0: U11.9 (DAT[0]); also elsewhere on the board
RPIA_MUX2_SD_D1: U11.10 (DAT[1]); also elsewhere on the board
RPIA_MUX2_SD_D2: U11.3 (DAT[2]); also elsewhere on the board
RPIA_MUX2_SD_D3: U11.4 (DAT[3]); also elsewhere on the board
RPIA_RUN: C2.1, IC4.4 (O), PIA_RUN.P$1, R73.1; also elsewhere on the board
RPIA_SD_SEL: IC7.5 (Q), PIA_SD_SEL.P$1, R66.1, R68.1, U11.11 (S), U14.11 (S)
RPIB_MUX1_SD_CLK: U4.8 (CLK); also elsewhere on the board
RPIB_MUX1_SD_CMD: U4.5 (CMD); also elsewhere on the board
RPIB_MUX1_SD_D0: U4.9 (DAT[0]); also elsewhere on the board
RPIB_MUX1_SD_D1: U4.10 (DAT[1]); also elsewhere on the board
RPIB_MUX1_SD_D2: U4.3 (DAT[2]); also elsewhere on the board
RPIB_MUX1_SD_D3: U4.4 (DAT[3]); also elsewhere on the board
RPIB_MUX2_SD_CLK: U13.8 (CLK); also elsewhere on the board
RPIB_MUX2_SD_CMD: U13.5 (CMD); also elsewhere on the board
RPIB_MUX2_SD_D0: U13.9 (DAT[0]); also elsewhere on the board
RPIB_MUX2_SD_D1: U13.10 (DAT[1]); also elsewhere on the board
RPIB_MUX2_SD_D2: U13.3 (DAT[2]); also elsewhere on the board
RPIB_MUX2_SD_D3: U13.4 (DAT[3]); also elsewhere on the board
RPIB_RUN: C1.1, IC5.4 (O), PIB_RUN.P$1, R74.1; also elsewhere on the board
RPIB_SD_SEL: IC7.9 (Q), PIB_SD_SEL.P$1, R67.1, R69.1, U4.11 (S), U13.11 (S)
RPI_PWR_SEL: IC4.1 (I0), IC6.2 (I), PI_PWR_SEL.P$1, R3.1, R5.1, R7.1, R88.1; also elsewhere on the board
WD_A_WDI: U5.4 (WDI), WD_A_WDI.TP; also elsewhere on the board
WD_B_WDI: U6.4 (WDI), WD_B_WDI.TP; also elsewhere on the board

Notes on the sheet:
Filter noise on run line; soft shutdown
route close to RPI!
ensure RESET is buffered

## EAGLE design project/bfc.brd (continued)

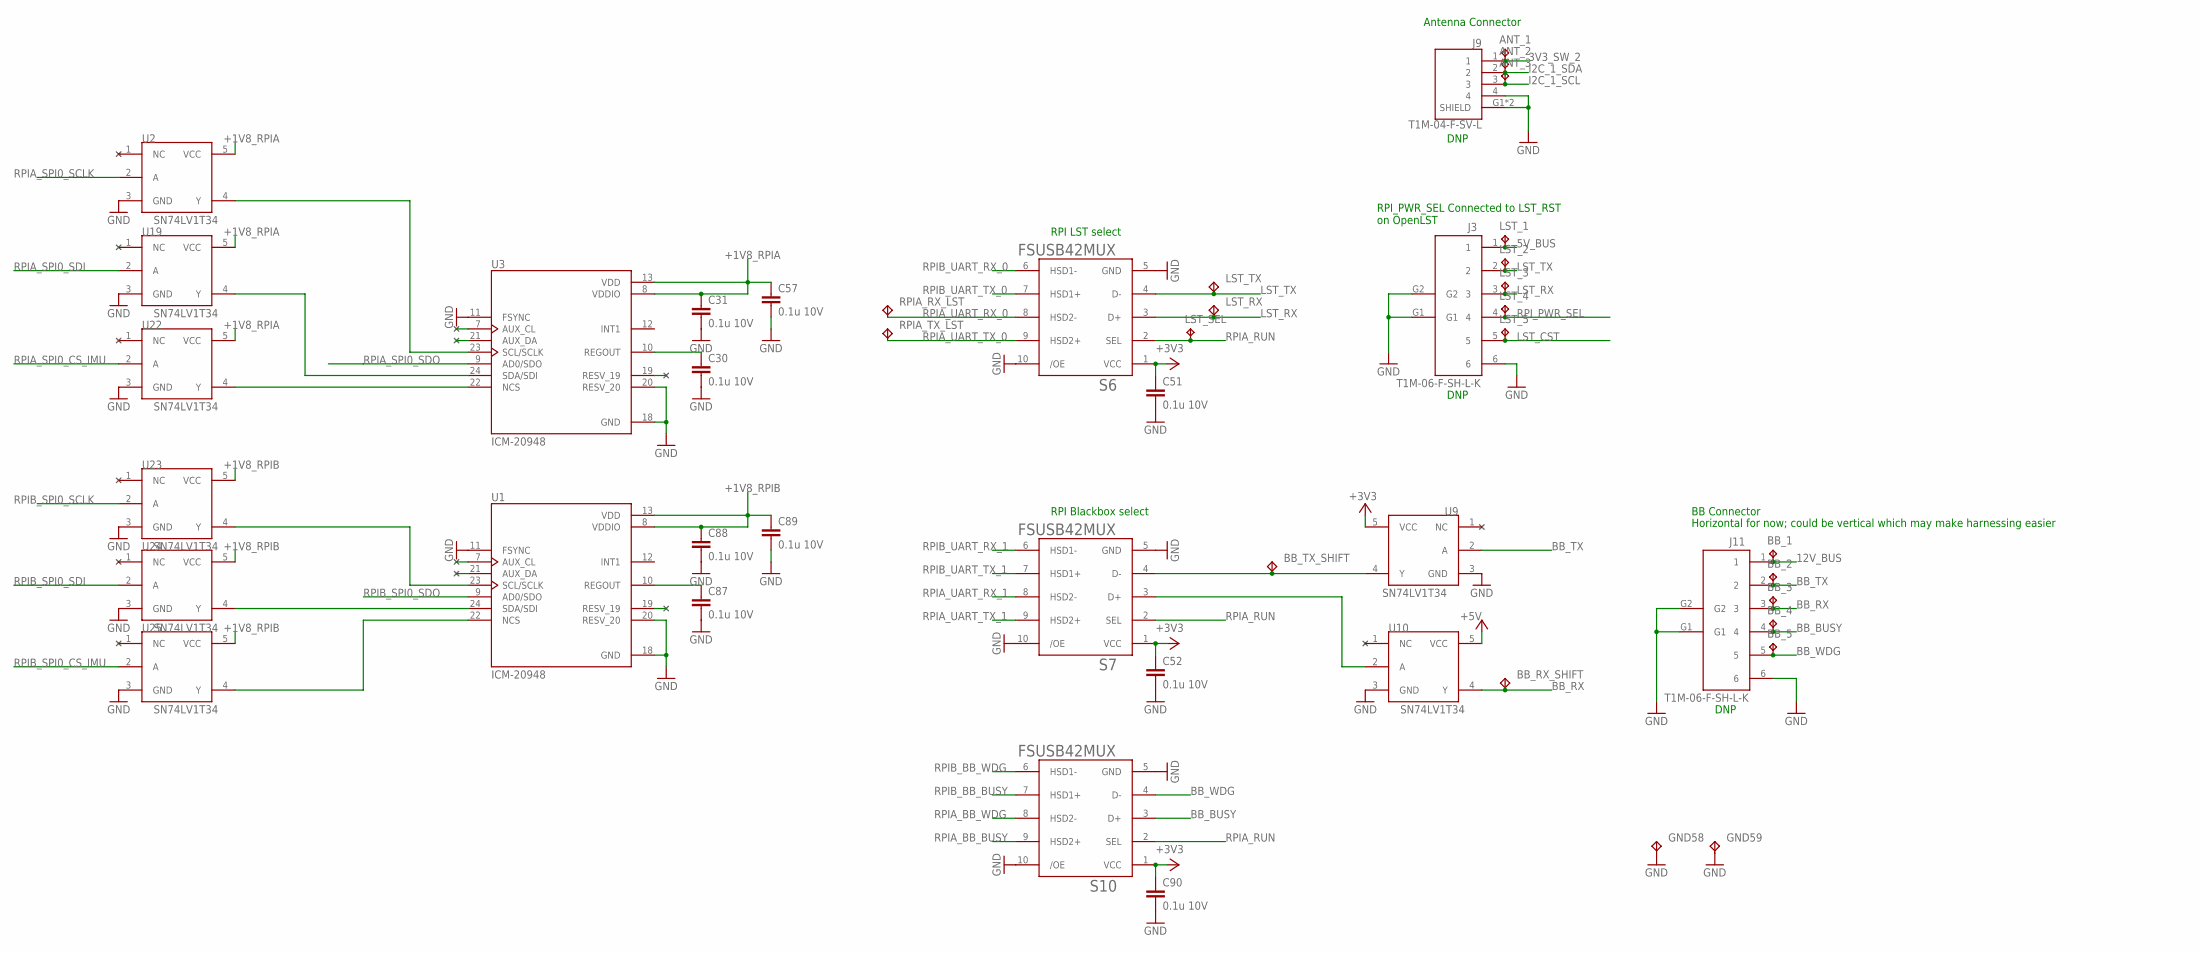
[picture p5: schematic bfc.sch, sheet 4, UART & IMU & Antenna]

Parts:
ANT_1, ANT_2, ANT_3: TPTP18SQ; TP18SQ
BB_1, BB_2, BB_3, BB_4, BB_5: TPTP18SQ; TP18SQ
BB_RX_SHIFT: TP_HRWN
BB_TX_SHIFT: TP_HRWN; MPN S2751-46R
C30, C31, C51, C52, C57, C87, C88, C89, C90: 0.1u 10V; C0603
GND58, GND59: TP_HRWN; MPN S2751-46R
J3, J11: T1M-06-F-SH-L-K; MPN T1M-06-F-SH-L
J9: T1M-04-F-SV-L; SAMTEC_T1M-04-F-SV-L; MPN T1M-04-F-SV-L
LST_1, LST_2, LST_3, LST_4, LST_5: TPTP15SQ; TP15SQ
LST_RX: TP_HRWN; MPN S2751-46R
LST_SEL: TPB1,27; B1,27
LST_TX: TP_HRWN; MPN S2751-46R
RPIA_RX_LST: TP_HRWN; MPN S2751-46R
RPIA_TX_LST: TP_HRWN; MPN S2751-46R
S6, S7, S10: FSUSB42MUX; MPN FSUSB42MUX
U1, U3: ICM-20948; QFN40P300X300X105-24N; MPN ICM-20948
U2, U9, U10, U19, U22, U23, U24, U25: SN74LV1T34; SOT23-5; MPN SN74LV1T34DBVR

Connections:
3V3_SW_2: ANT_1.TP, J9.1; also elsewhere on the board
5V_BUS: J3.1, LST_1.TP; also elsewhere on the board
12V_BUS: BB_1.TP, J11.1; also elsewhere on the board
+1V8_RPIA: C31.1, C57.1, U2.5 (VCC), U3.8 (VDDIO), U3.13 (VDD), U19.5 (VCC), U22.5 (VCC); also elsewhere on the board
+1V8_RPIB: C88.1, C89.1, U1.8 (VDDIO), U1.13 (VDD), U23.5 (VCC), U24.5 (VCC), U25.5 (VCC); also elsewhere on the board
+3V3: C51.1, C52.1, C90.1, S6.1 (VCC), S7.1 (VCC), S10.1 (VCC), U9.5 (VCC); also elsewhere on the board
+5V: U10.5 (VCC); also elsewhere on the board
BB_BUSY: BB_4.TP, J11.4, S10.3 (D+)
BB_RX: BB_3.TP, BB_RX_SHIFT.P$1, J11.3, U10.4 (Y)
BB_TX: BB_2.TP, J11.2, U9.2 (A)
BB_WDG: BB_5.TP, J11.5, S10.4 (D-)
GND: C30.2, C31.2, C51.2, C52.2, C57.2, C87.2, C88.2, C89.2, C90.2, GND58.P$1, GND59.P$1, J3.6, J3.G1, J3.G2, J9.4, J9.G1 (SHIELD), J9.G2 (SHIELD), J11.6, J11.G1, J11.G2, S6.5 (GND), S6.10 (/OE), S7.5 (GND), S7.10 (/OE), S10.5 (GND), S10.10 (/OE), U1.11 (FSYNC), U1.18 (GND), U1.20 (RESV_20), U2.3 (GND), U3.11 (FSYNC), U3.18 (GND), U3.20 (RESV_20), U9.3 (GND), U10.3 (GND), U19.3 (GND), U22.3 (GND), U23.3 (GND), U24.3 (GND), U25.3 (GND); also elsewhere on the board
I2C_1_SCL: ANT_3.TP, J9.3; also elsewhere on the board
I2C_1_SDA: ANT_2.TP, J9.2; also elsewhere on the board
LST_CST: J3.5, LST_5.TP
LST_RX: J3.3, LST_3.TP, LST_RX.P$1, S6.3 (D+)
LST_TX: J3.2, LST_2.TP, LST_TX.P$1, S6.4 (D-)
unnamed: C87.1, U1.10 (REGOUT)
unnamed: U2.4 (Y), U3.23 (SCL/SCLK)
unnamed: U3.24 (SDA/SDI), U19.4 (Y)
unnamed: U3.22 (NCS), U22.4 (Y)
unnamed: U1.23 (SCL/SCLK), U23.4 (Y)
unnamed: U1.22 (NCS), U25.4 (Y)
unnamed: U1.24 (SDA/SDI), U24.4 (Y)
unnamed: C30.1, U3.10 (REGOUT)
unnamed: BB_TX_SHIFT.P$1, S7.4 (D-), U9.4 (Y)
unnamed: S7.3 (D+), U10.2 (A)
RPIA_BB_BUSY: S10.9 (HSD2+); also elsewhere on the board
RPIA_BB_WDG: S10.8 (HSD2-); also elsewhere on the board
RPIA_RUN: LST_SEL.TP, S6.2 (SEL), S7.2 (SEL), S10.2 (SEL); also elsewhere on the board
RPIA_SPI0_CS_IMU: U22.2 (A); also elsewhere on the board
RPIA_SPI0_SCLK: U2.2 (A); also elsewhere on the board
RPIA_SPI0_SDI: U19.2 (A); also elsewhere on the board
RPIA_SPI0_SDO: U3.9 (AD0/SDO); also elsewhere on the board
RPIA_UART_RX_0: RPIA_RX_LST.P$1, S6.8 (HSD2-); also elsewhere on the board
RPIA_UART_RX_1: S7.8 (HSD2-); also elsewhere on the board
RPIA_UART_TX_0: RPIA_TX_LST.P$1, S6.9 (HSD2+); also elsewhere on the board
RPIA_UART_TX_1: S7.9 (HSD2+); also elsewhere on the board
RPIB_BB_BUSY: S10.7 (HSD1+); also elsewhere on the board
RPIB_BB_WDG: S10.6 (HSD1-); also elsewhere on the board
RPIB_SPI0_CS_IMU: U25.2 (A); also elsewhere on the board
RPIB_SPI0_SCLK: U23.2 (A); also elsewhere on the board
RPIB_SPI0_SDI: U24.2 (A); also elsewhere on the board
RPIB_SPI0_SDO: U1.9 (AD0/SDO); also elsewhere on the board
RPIB_UART_RX_0: S6.6 (HSD1-); also elsewhere on the board
RPIB_UART_RX_1: S7.6 (HSD1-); also elsewhere on the board
RPIB_UART_TX_0: S6.7 (HSD1+); also elsewhere on the board
RPIB_UART_TX_1: S7.7 (HSD1+); also elsewhere on the board
RPI_PWR_SEL: J3.4, LST_4.TP; also elsewhere on the board

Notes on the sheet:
RPI LST select
RPI Blackbox select
RPI_PWR_SEL Connected to LST_RST on OpenLST
Antenna Connector
BB Connector
Horizontal for now; could be vertical which may make harnessing easier
DNP

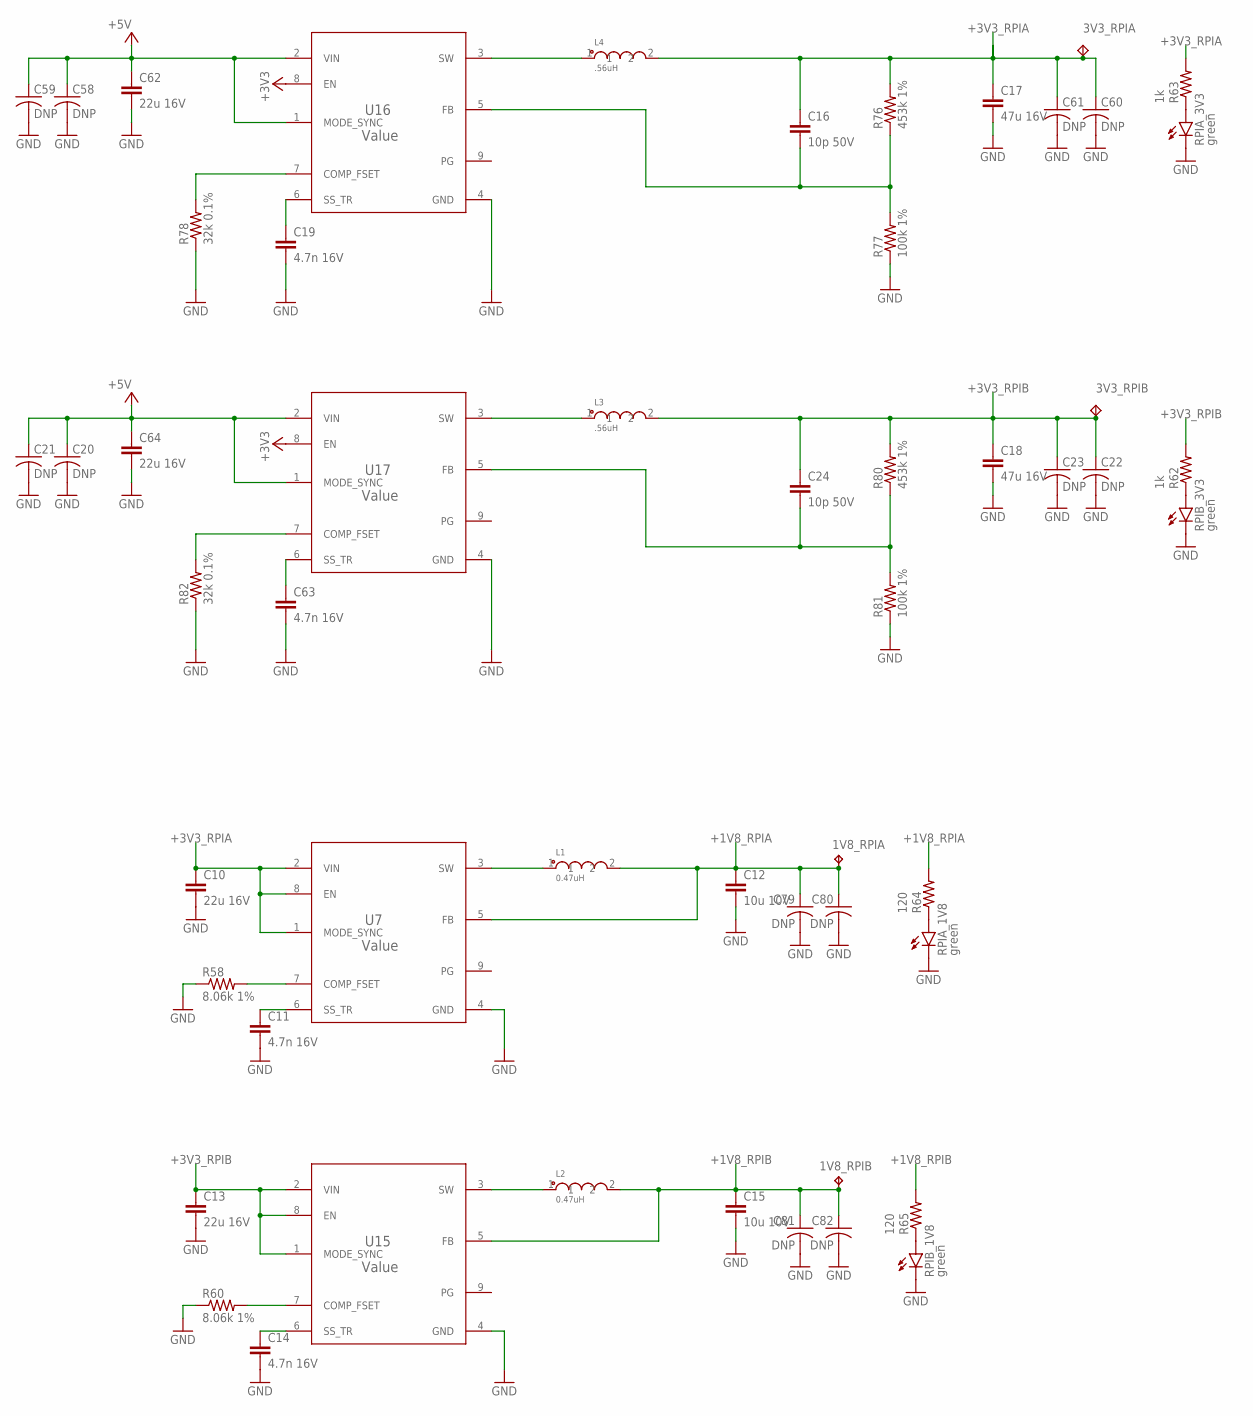
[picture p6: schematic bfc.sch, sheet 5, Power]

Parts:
1V8_RPIA, 1V8_RPIB: TPB1,27; B1,27
3V3_RPIA, 3V3_RPIB: TP_HRWN; MPN S2751-46R
C10, C13, C62, C64: 22u 16V; C1206
C11, C14, C19, C63: 4.7n 16V; C0603
C12, C15: 10u 10V; C1206
C16, C24: 10p 50V; C0603
C17, C18: 47u 16V; C1210
C20, C21, C22, C23, C58, C59, C60, C61, C79, C80, C81, C82: DNP; C0805
L1, L2: 0.47uH; LPS3010; MPN LPS3010-471MRC
L3, L4: .56uH; INDP_LPS4018-472MRB; MPN LPS4018-561MRC
R58, R60: 8.06k 1%; R0603
R62, R63: 1k; R0603
R64, R65: 120; R0603
R76, R80: 453k 1%; R0603
R77, R81: 100k 1%; R0603
R78, R82: 32k 0.1%; R0603
RPIA_1V8: green; SML0603; MPN LG L29K-F2J1-24-Z
RPIA_3V3: green; SML0603; MPN 150060VS75000
RPIB_1V8: green; SML0603; MPN LG L29K-F2J1-24-Z
RPIB_3V3: green; SML0603; MPN 150060VS75000
U7, U15: Value; RWY0009A; MPN TPS628112MQWRWYRQ1
U16, U17: Value; RWY0009A; MPN TPS62812QWRWYRQ1

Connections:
1: C24.2, R80.1, R81.2, U17.5 (FB)
2: C16.2, R76.1, R77.2, U16.5 (FB)
3: L3.1, U17.3 (SW)
7: L4.1, U16.3 (SW)
+1V8_RPIA: 1V8_RPIA.TP, C12.1, C79.1, C80.1, L1.2, R64.2, U7.5 (FB); also elsewhere on the board
+1V8_RPIB: 1V8_RPIB.TP, C15.1, C81.1, C82.1, L2.2, R65.2, U15.5 (FB); also elsewhere on the board
+3V3: U16.8 (EN), U17.8 (EN); also elsewhere on the board
+3V3_RPIA: 3V3_RPIA.P$1, C10.1, C16.1, C17.1, C60.1, C61.1, L4.2, R63.2, R76.2, U7.1 (MODE_SYNC), U7.2 (VIN), U7.8 (EN); also elsewhere on the board
+3V3_RPIB: 3V3_RPIB.P$1, C13.1, C18.1, C22.1, C23.1, C24.1, L3.2, R62.2, R80.2, U15.1 (MODE_SYNC), U15.2 (VIN), U15.8 (EN); also elsewhere on the board
+5V: C20.1, C21.1, C58.1, C59.1, C62.1, C64.1, U16.1 (MODE_SYNC), U16.2 (VIN), U17.1 (MODE_SYNC), U17.2 (VIN); also elsewhere on the board
GND: C10.2, C11.2, C12.2, C13.2, C14.2, C15.2, C17.2, C18.2, C19.2, C20.2, C21.2, C22.2, C23.2, C58.2, C59.2, C60.2, C61.2, C62.2, C63.2, C64.2, C79.2, C80.2, C81.2, C82.2, R58.1, R60.1, R77.1, R78.1, R81.1, R82.1, RPIA_1V8.C, RPIA_3V3.C, RPIB_1V8.C, RPIB_3V3.C, U7.4 (GND), U15.4 (GND), U16.4 (GND), U17.4 (GND); also elsewhere on the board
unnamed: R78.2, U16.7 (COMP_FSET)
unnamed: C19.1, U16.6 (SS_TR)
unnamed: R82.2, U17.7 (COMP_FSET)
unnamed: C63.1, U17.6 (SS_TR)
unnamed: C11.1, U7.6 (SS_TR)
unnamed: R58.2, U7.7 (COMP_FSET)
unnamed: L1.1, U7.3 (SW)
unnamed: R60.2, U15.7 (COMP_FSET)
unnamed: C14.1, U15.6 (SS_TR)
unnamed: L2.1, U15.3 (SW)
unnamed: R62.1, RPIB_3V3.A
unnamed: R63.1, RPIA_3V3.A
unnamed: R64.1, RPIA_1V8.A
unnamed: R65.1, RPIB_1V8.A

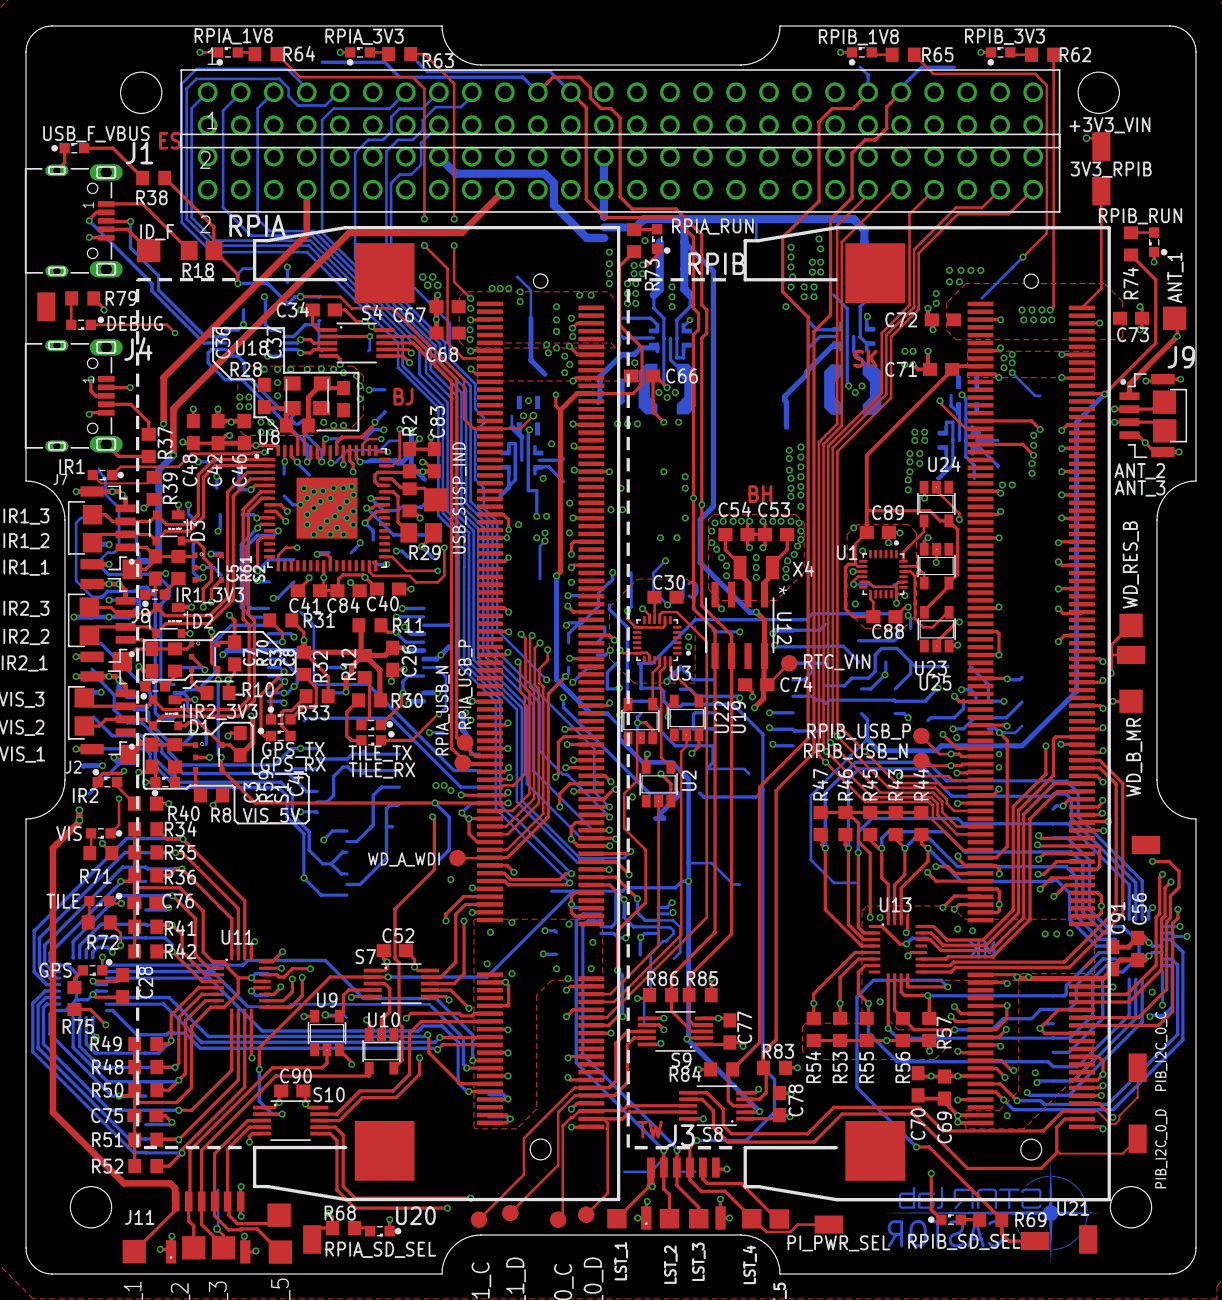
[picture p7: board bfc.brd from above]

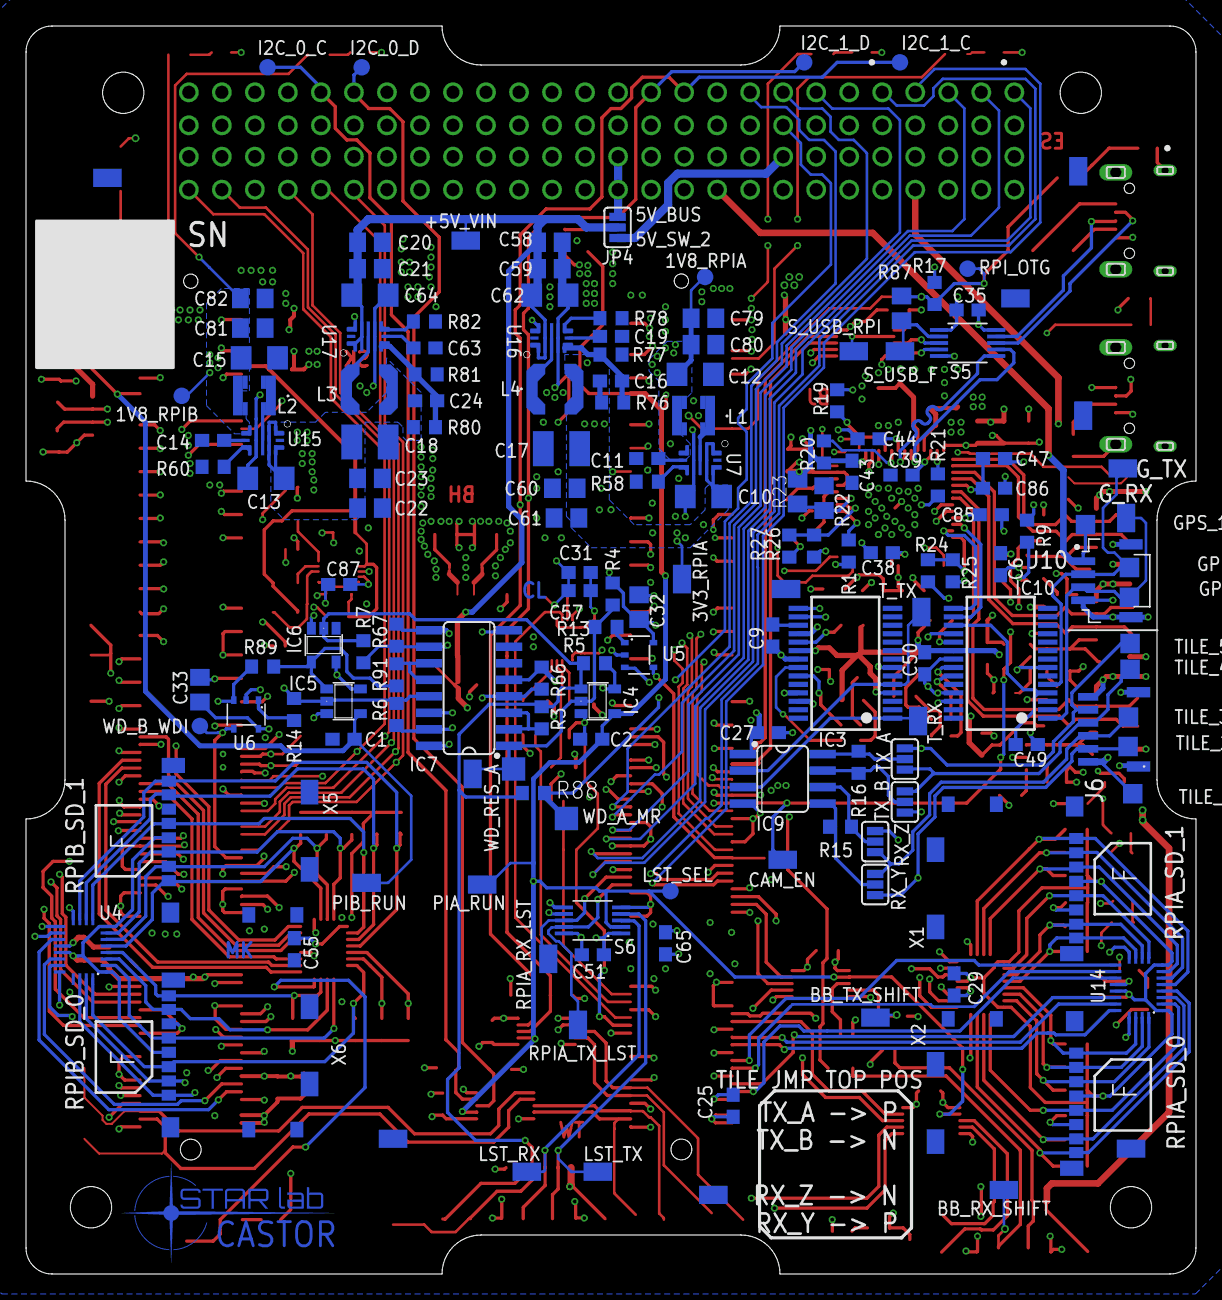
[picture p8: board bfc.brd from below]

Board: 6 copper layers, 90.0 x 96.0 mm, 366 parts (163 on the bottom side), 251 nets.

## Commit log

2020-05-15 Added schematic and board from most recent build
    Only change from most recent build is the MPN for the JK flip flop, since part number did not match footprint
    [bfc.brd, bfc.sch]
2020-05-15 fixed 1 DRC error. Trace dragged over pad accidentally during previous brd viewing
    [bfc.brd]
2020-07-02 removed protected graphics on bottom of board
    [bfc.brd]

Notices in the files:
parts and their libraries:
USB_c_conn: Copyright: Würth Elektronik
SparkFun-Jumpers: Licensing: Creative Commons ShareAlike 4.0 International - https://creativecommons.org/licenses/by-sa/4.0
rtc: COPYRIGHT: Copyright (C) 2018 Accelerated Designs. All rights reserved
